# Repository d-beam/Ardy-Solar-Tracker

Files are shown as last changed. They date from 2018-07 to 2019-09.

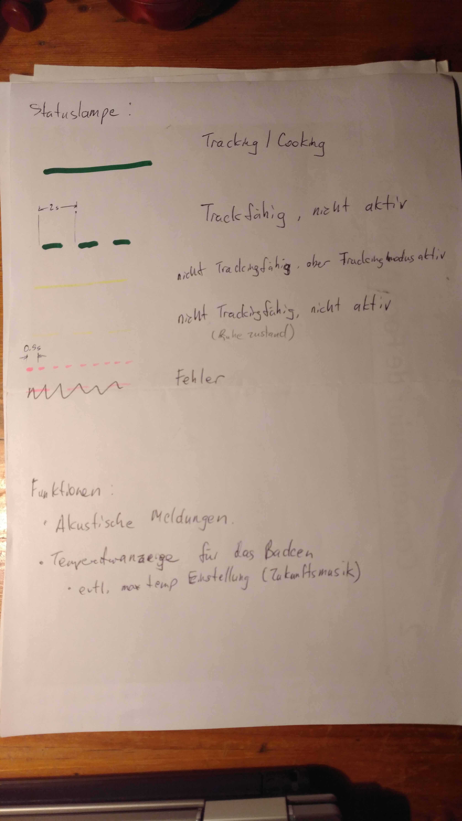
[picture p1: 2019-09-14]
docs/concepts/UI concept statusLED.jpg

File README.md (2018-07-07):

# Ardy-Solar-Tracker
2-axis Solar Tracker for concentrators and mirrors, supporting alt-az and Fixed Equatorial mechanisms, safe position

This project is started in June 2018 by the Technology Group at the Temera Healing Biotope in Colos, Portugal.  It is a Arduino based solar tracking controller with the following software features:

# Features
* support 2 axes, configurable also for use with only 1 (X) axis.
* support mechanisms working with Alt-Az or fixed equatorial coordinants and actuators
* support configuration of absolute positioning (open-loop), using only limit switches as positional feedback.
** Configuration of real time/date and installation orientation (home position) required.
* for each axis, read analog signals from 2 photodiodes and a signal representing the difference of the two diode signals for closed-loop control
* switch between open-loop and closed-loop control based on the reliability of the sensor signal
* Usage Modes: Idle, Tracking on, safe position
* automatically disable tracking below a certain elevation, or outside a defined range in hour-angle
* sensor polarity inversion, configurable
* travel limit switches, configurable as normally open or normally closed
* inversion of the orientation of each push button pair for each axis, configurable
* 2 speeds of motor control, with configurable dead bands
* push buttons for manual movements
* Modularity to allow changing motor controllers or RTC modules

It is written in Arduino code, but also with some C concepts such as pointers,
functions with pointer arguements, etc.

# Suggested Improvements:
* split up source code into multiple files for logical modularity
* improve very rough position estimator, which integrates the movement command over time for a positional change.
* add configurable offset for differential sensor signals

# Future directions:
* As solar cooking controller: setting of cooking time and maximum temperature
* logging of solar intensity

Contact Daniel Müller <dbmueller@gmx.net> for more information about the project, including the related electronics hardware.

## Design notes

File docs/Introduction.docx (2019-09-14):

# Open Source Solar Tracker

In the frame of a four-week technology seminar in Tamera Greg Fung, Christian Oekermann and Daniel Müller started the development of a microcontroller-based solar tracker.

The interest in that topic in Tamera mainly was raised from the Tamera-FixFocus project, where an analog sensor and electronics were used to control the two axis of the solar concentrator. This setup was limited in functionality and a digital modular solution based on the popular Arduino platform seem to be a good way to go forward.

Beside industrial applications the interest for solar tracking controllers also expands to other application fields, mainly towards solar cooking. Several tracked solar cookers are currently in use in Tamera and potentially could be controlled by the very same system to improve the usability greatly.

# General features

- 12-24 V input voltage
- Arduino based
- Modular system - Control board, motor drivers, real-time clock easily exchangeable
- Controles two axes (configurable for mounts based on Horizontal or equatorial coordinate systems)
- Homing with limit switches
- Support of different motor types (e.g. DC motors, stepper motors)
- Two stage tracking: Rough positioning by sun position algorithm when the sun doesn’t shine (open-loop control) and accurate tracking with photodiode sensor (closed-loop control) when the sun shines

# First application - Solar Tracker v0.1

The first implementation of the system is pretty much a copy of the analog tracking control system previously with the Tamera-FixFocus solar concentrator, but now comes with the capability of both closed-loop (sensor) tracking mode and open-loop tracking mode (using the sun position algorithm).

Download the files here

Discuss with the community here

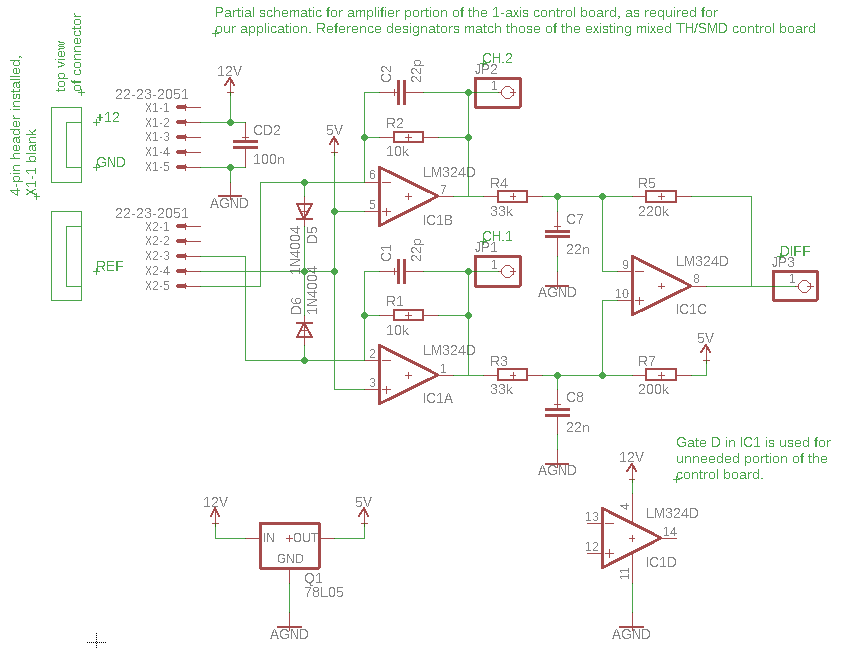
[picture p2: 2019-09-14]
docs/electronics/Sensor interface/sensor_interface_board_schematic.png

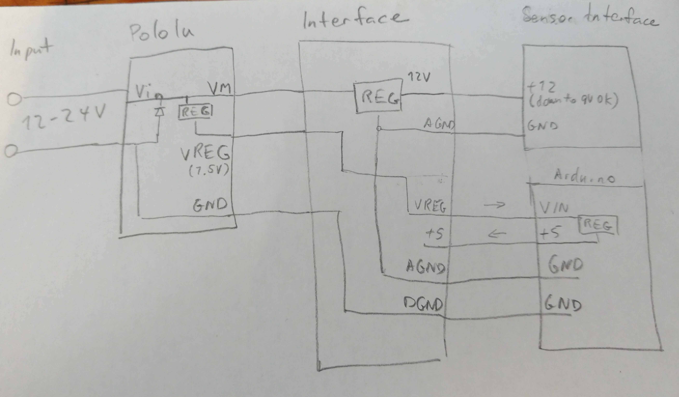
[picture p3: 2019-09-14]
docs/pictures/power concept.jpg

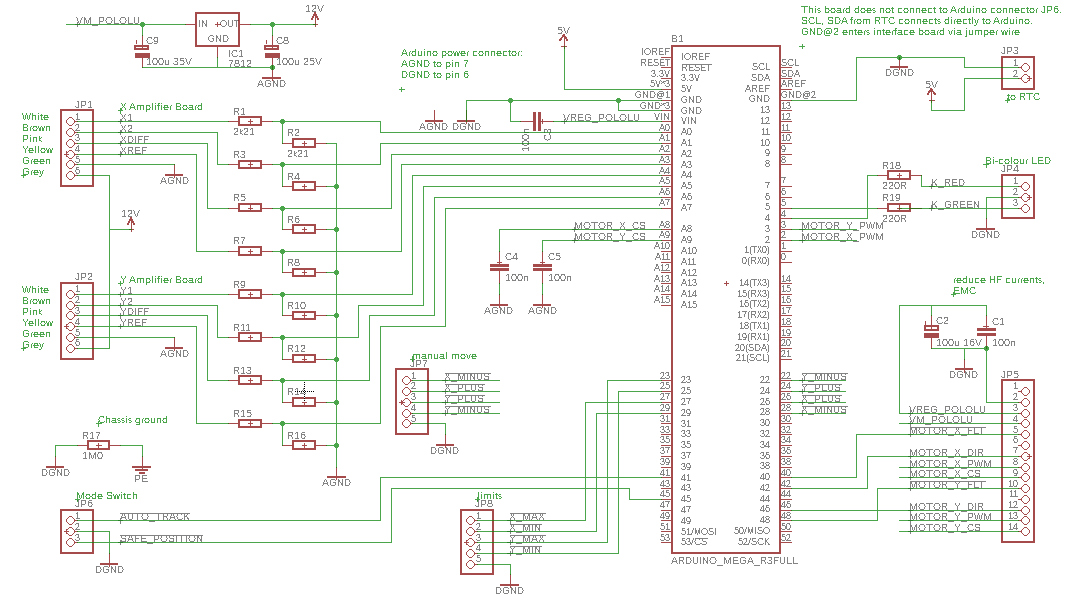
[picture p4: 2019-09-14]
docs/electronics/Interface shield/interface_board_schematic_v0_1.png

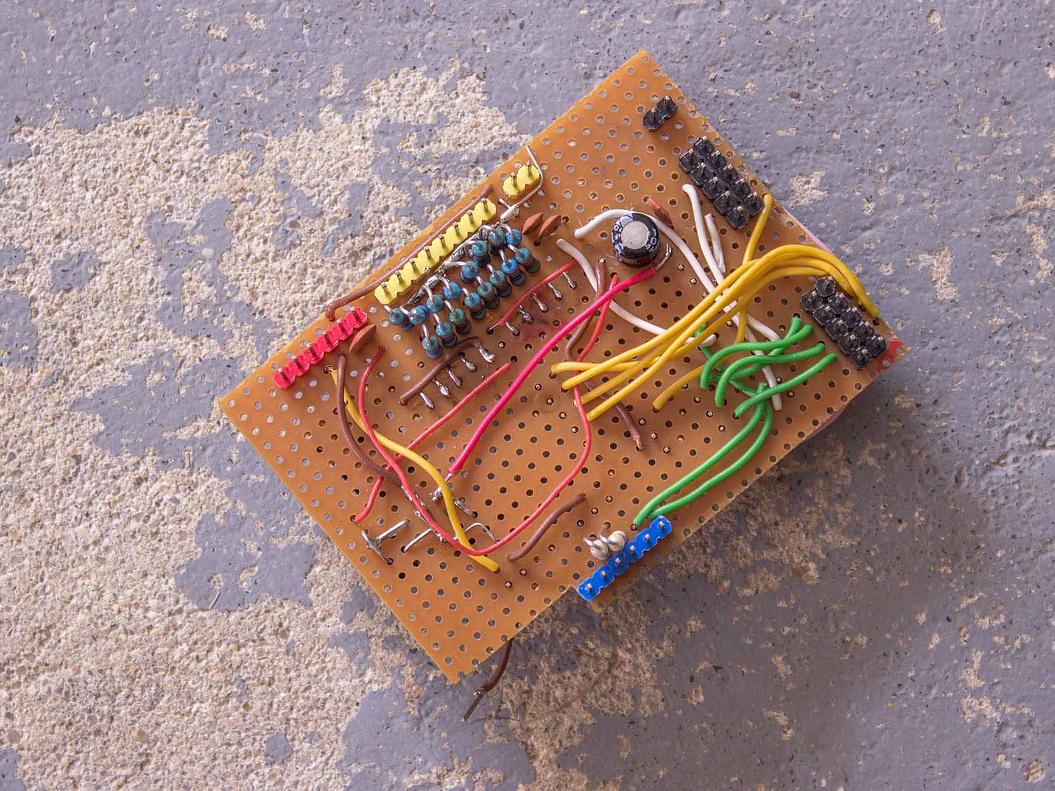
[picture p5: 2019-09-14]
docs/pictures/board_back.jpg

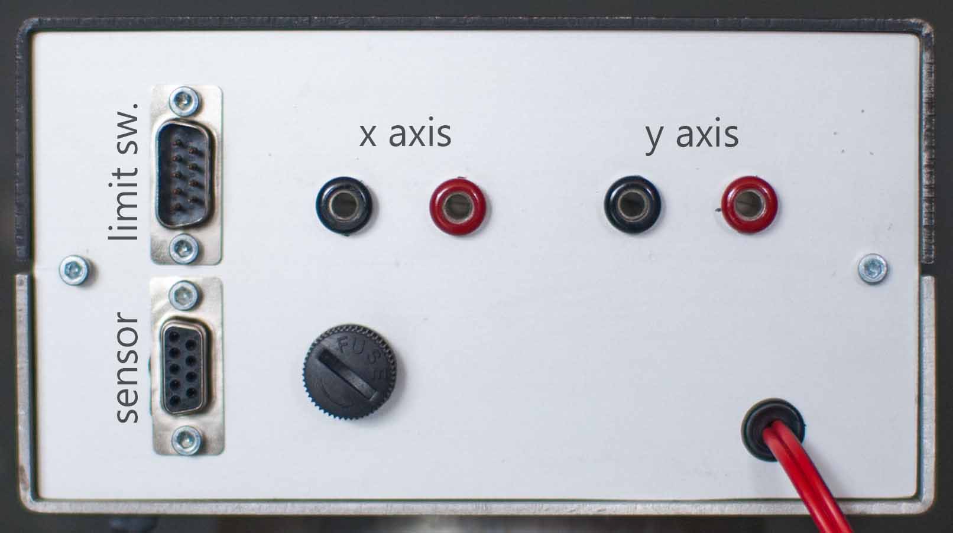
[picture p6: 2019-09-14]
docs/pictures/panel_front.jpg

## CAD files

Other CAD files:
docs/CAD models/Sensor.f3d

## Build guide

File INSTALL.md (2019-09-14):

Install/Build Instructions you will find in the docs folder

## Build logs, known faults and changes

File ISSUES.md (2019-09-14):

known issues 

21.03.2019
- When clouds come in, the mirror will move quite a bit, trying to “follow the sun”, before it switches to

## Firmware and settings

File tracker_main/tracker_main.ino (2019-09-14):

/******************************************************************************
    Solar Tracker: Application for Arduino
    settings for Tamera FixedFocus Mirror
    July 7, 2018 15:15 2018

    Update on 13.9.2019 
    - split into diffrent files 
     
    Gregory Fung <gwfung@gmail.com>
    Free for use under Creative Commons license CC BY:
   https://creativecommons.org/licenses/
 *****************************************************************************/
#include "DualG2HighPowerMotorShield.h"

#include <Wire.h>
#include <RTClib.h>
#include <math.h>
#include <Helios.h>   // Heliostat / Sun location library

// Local configuration
// Tamera: 37° 43' 7.2001'' N, 8° 31' 14.1924'' W
#define LATITUDE      37.7186667f     // [-90..90]
#define LONGITUDE     -8.520609f      // [-180..180)

// Application mode and settings --------------------
#define EQUATORIAL_AXES_MODE      true  // if false, output channels are Azimuth and elevation
// if false, output channels are X= tau hour angle and Y= delta declination
#define Y_AXIS_ACTIVE           true  // if false, all control functions except manual move is disabled for Y

#define OPEN_LOOP_POSITIONING_ENABLE  true  // if false, safe position and position initialization disabled.
// only tracking after rough manual alignment supported.

// Home position at min or max limit -----------
// true: homing at maximum position
// false: homing at mininum position
#define HOME_AT_MAX_X         false // morning, min tau position
#define HOME_AT_MAX_Y         true  // physically lowest position: summer, max delta

// Home position: --------------------
// The position of the system with minimum X and Y values, just before the limit switches are actuated.
// if EQUATORIAL_AXES_MODE, X is hour angle, Y is inclination
// if !EQUATORIAL_AXES_MODE, X is Azimuth, Y is elevation
#if EQUATORIAL_AXES_MODE
  #define HOME_POSITION_X           (-91.0) // °, morning position where low limit switches are located
  #define HOME_POSITION_Y           (23.5)  // ° where low limit switches are located
#else
  #define HOME_POSITION_X           (0.0)   // ° (north)
  #define HOME_POSITION_Y           (10.0)  // ° where low limit switches are located
#endif

// Safe position: --------------------
//Position for safe mode.  Must be within travel limits
#if EQUATORIAL_AXES_MODE
  #define SAFE_POSITION_X           (-90.0) // °
  #define SAFE_POSITION_Y           (23.0)  // °
#else
  #define SAFE_POSITION_X           (5.0)   // °
  #define SAFE_POSITION_Y           (11.0)  // °
#endif

// tracking active limitations: --------------------
// tracking will deactivate when the sun is calculated to be outside these ranges
#define SUN_ELEVATION_MIN_FOR_TRACKING      (10.0)  // °
#define SUN_HOUR_ANGLE_MIN_FOR_TRACKING     (-85.0) // °
#define SUN_HOUR_ANGLE_MAX_FOR_TRACKING     (85.0)  // °

// Manual move button polarity: --------------------
#define MANUAL_MOVE_POLARITY_FLIP_X       false   // true to invert control response, false otherwise
#define MANUAL_MOVE_POLARITY_FLIP_Y       true    // true to invert control response, false otherwise

// Limit switch action: --------------------
#define X_LIMIT_TRIP_SWITCH_N_O     true    // true: normally open switch, closes at limit
#define Y_LIMIT_TRIP_SWITCH_N_O     true    // true: normally open switch, closes at limit

// Sensor polarity: --------------------
#define SENSOR_POLARITY_FLIP_X      false   // true to invert control response, false otherwise
#define SENSOR_POLARITY_FLIP_Y      true    // true to invert control response, false otherwise

// Closed loop position sanity check: -------------------
#define CLOSED_LOOP_POSITIONING_SANITY_CHECK (false)      // true to enable comparison with calculated position

// Open loop position estimate: --------------------------
// Currently: Rectangular integration of motor movements commands
// set the steady-state movement speeds here, in °/s
#define MOTOR_SPEED_SLOW_PER_SEC_X      ((MOTOR_SPEED_FAST_PER_SEC_Y * POLOLU_SPEED_SLOW_Y) / POLOLU_SPEED_FAST_Y)    // speed ratiometric to Speed command?
#define MOTOR_SPEED_FAST_PER_SEC_X      0.54f   // °/s.  probably 10% accurate, needs further calibration
#define MOTOR_SPEED_SLOW_PER_SEC_Y      ((MOTOR_SPEED_FAST_PER_SEC_Y * POLOLU_SPEED_SLOW_Y) / POLOLU_SPEED_FAST_Y)    // °/s
#define MOTOR_SPEED_FAST_PER_SEC_Y      0.26f   // °/s.  probably 40% accurate, needs further calibration

// Control deadbands: --------------------------
// This reduces continual back and forth dithering due to slack in mechanical mechanism
//
// FAST_MOVE_DEADBAND: Within this much of the target location, stop using fast move speed
// CONTROL_DEADBAND: Within this much of the target location, stop moving
#define OPEN_LOOP_FAST_MOVE_DEADBAND_X    3   // °.
#define OPEN_LOOP_CONTROL_DEADBAND_X    0.3   // °
#define CLOSED_LOOP_FAST_MOVE_DEADBAND_X  500 // in raw diff ADC units (total range 2048, more than 1500 not recommended)
// Big setting to allow mechanism to decellerate and not overshoot
#define CLOSED_LOOP_CONTROL_DEADBAND_X    50    // in raw diff ADC units (total range 2048, more than 1500 not recommended)
#define CLOSED_LOOP_ABORT_LIMIT_X         25    // °, used for sanity check

#define OPEN_LOOP_FAST_MOVE_DEADBAND_Y    2   // °
#define OPEN_LOOP_CONTROL_DEADBAND_Y    0.3   // °
#define CLOSED_LOOP_FAST_MOVE_DEADBAND_Y  500 // in raw diff ADC units (total range 2048, more than 1500 not recommended)
#define CLOSED_LOOP_CONTROL_DEADBAND_Y    50  // in raw diff ADC units (total range 2048, more than 1500 not recommended)
#define CLOSED_LOOP_ABORT_LIMIT_Y         25  // °, used for sanity check


// movement delays: -------------------
// after stopping drive motors, how long to wait for mechanism to stop before proceeding
#define MOVE_STOP_FROM_FAST_DELAY (1000)    // ms
#define MOVE_STOP_FROM_SLOW_DELAY (1000)    // ms

// Closed loop tracking: -------------------
#define TRACKING_STABLE_COUNT       5       // count of loops before tracking stable is declared
                                            // used for position calibration

// Computation times: -------------------
// These constants may be used to integrate speed over time for position estimates
//
// Normal computation: happens every cycle of loop()
#define NORMAL_COMPUTATION_MS       (50)    // measured computational duration
// Extended computation: happens occassionally
#define EXTENDED_COMPUTATION_MS     (400)   // measured computational duration

// ******************************************************************************
// constants for internal operations, usually does not change between application
// ******************************************************************************

// Delay at the end of loop() before next cycle
#define UPDATE_DELAY_MS                 (250)
#define EXTENDED_COMPUTATION_COUNT      (60)

// Sensor limits, in raw 12-bit ADC units ------------
// ABS_MIN: below this level, sensor reading is not used.
//   lower to allow more tracking even if full cloudy,
//   may cause problems with background light when pointed away from sun
//   raise to use open loop calculated more often when cloudy
#define SENSOR_ABS_MIN      300       // 250 accepts signal levels when cloudy
                                      //~900 have been seen in full sun
// ABS_MAX: unrealistically strong sensor level
#define SENSOR_ABS_MAX      1800      // set >4096 to effectively disable checking
// REF: reference level of analog circuitry, which is also read by an ADC channel
#define SENSOR_REF_DEFAULT  2048      // half of full scale
#define SENSOR_REF_MAX      2248      // min resaonable ref value
#define SENSOR_REF_MIN      1848      //

// Initialization ------------
// This many loops are ran before tracking will begin, to allow analog inputs to settle.
#define SENSOR_INIT_LOOP_COUNT    (16)

// Arduino GPIO numbers: analog inputs ----------------
#define AI_X1ABS            0
#define AI_X2ABS            1
#define AI_XDIFF            2
#define AI_XREF             3
#define AI_Y1ABS            4
#define AI_Y2ABS            5
#define AI_YDIFF            6
#define AI_YREF             7
#define AI_MOTOR_CURRENT_X  8
#define AI_MOTOR_CURRENT_Y  9

// Arduino GPIO numbers: digital ---------------
// 0, 1 used for serial comms
#define DO_MOTOR_PWM_X      2
#define DO_MOTOR_PWM_Y      3
#define DO_STATUS_LED_RED   4
#define DO_STATUS_LED_GREEN 5

#define DI_MODE_SAFE          43
#define DI_MODE_TRACK         41
#define DI_LIMIT_SWITCH_X_MAX 27
#define DI_LIMIT_SWITCH_X_MIN 29

//normal configration:
//#define DI_LIMIT_SWITCH_Y_MAX   23
//#define DI_LIMIT_SWITCH_Y_MIN   25
//compensating for wiring error on Tamera fixed-focus
#define DI_LIMIT_SWITCH_Y_MAX   25
#define DI_LIMIT_SWITCH_Y_MIN   23

#define DI_MANUAL_MOVE_X_PLUS   26
#define DI_MANUAL_MOVE_X_MINUS  28
#define DI_MANUAL_MOVE_Y_PLUS   24
#define DI_MANUAL_MOVE_Y_MINUS  22

// If motor PWM assignments match default config from
// pololu shield, timer1 can be used for PWM:  M1 9, M2 10
#define DO_MOTOR_DIR_X    42
#define DI_MOTOR_FAULT_X  40
#define DO_MOTOR_DIR_Y    46
#define DI_MOTOR_FAULT_Y  48

// unused, but referenced by motor driver
#define DO_MOTOR_SLEEP_X  47
#define DO_MOTOR_SLEEP_Y  45


// Serial Monitor debug output selection
// #define SERIAL_PLOTTER_FORMAT  // define for serial plotting csv format, disables labels
// #define SERIAL_DEBUG_RAW_SENSOR  // define to print raw sensor values
#define SERIAL_DEBUG_SUN_CALC   // define to enable

/******************************************************************************
   Global Variables
******************************************************************************/

// Using custom constructor here to specify non-default pin assignment
// Note the exact model of the sheild is in the type name and may need adjustment
// see https://github.com/pololu/dual-g2-high-power-motor-shield/
// TODO generic version DualG2HighPowerMotorShield?  current sensing gain info would not be encapsulated.
DualG2HighPowerMotorShield18v18 md(
  DO_MOTOR_SLEEP_X, DO_MOTOR_DIR_X,
  DO_MOTOR_PWM_X, DI_MOTOR_FAULT_X, AI_MOTOR_CURRENT_X,
  DO_MOTOR_SLEEP_Y, DO_MOTOR_DIR_Y,
  DO_MOTOR_PWM_Y, DI_MOTOR_FAULT_Y, AI_MOTOR_CURRENT_Y);
RTC_DS1307 rtc;
Helios sunPosition;

// actual date/time in UTC
DateTime actualTime;

// X axis---------------
int sensorX1RawAbs;
int sensorX2RawAbs;
int sensorXRawDiff;
int sensorXRawRef = SENSOR_REF_DEFAULT;
int sensorX1Level;
int sensorX2Level;
int sensorXDiff;
bool sensorLevelsOkX = false;
int motorSettingX = 0;
int motorCurrentX = 0;
bool atLimitXMax;
bool atLimitXMin;

bool closedLoopActiveX = false;
bool closedLoopFaultX = false;
bool trackingLockedX = false;
int trackingStableCounterX = 0;

double targetAzimuth;
float errorPositionX;     // position error for X in open loop mode
float actualPositionX;
double targetPositionX;
int errorClosedLoopX;     // control error for X, int because using raw ADC units


// Y axis--------------------
int sensorY1RawAbs;
int sensorY2RawAbs;
int sensorYRawDiff;
int sensorYRawRef = SENSOR_REF_DEFAULT;
int sensorY1Level;
int sensorY2Level;
int sensorYDiff;
bool sensorLevelsOkY = false;
int motorSettingY = 0;
int motorCurrentY = 0;
bool atLimitYMax;
bool atLimitYMin;

bool closedLoopActiveY = false;
bool closedLoopFaultY = false;
bool trackingLockedY = false;
int trackingStableCounterY = 0;

double targetElevation;
float errorPositionY;     // position error for Y in open loop mode
float actualPositionY;
double targetPositionY;
int errorClosedLoopY;     // control error for Y, int because using raw ADC units


// both axis--------------------
bool sensorInitDone = false;
bool generalFault = false;
bool userInputFault = false;
bool trackingRequested = false;   // user input
bool trackingActive = false;    // possible and active
bool safePositionCmd = false;
bool positionInitialized = false;
bool manualMoveXPlus = false;
bool manualMoveXMinus = false;
bool manualMoveYPlus = false;
bool manualMoveYMinus = false;
int slowUpdateCountdown = 0;

// LED
#define LED_COLOUR_OFF    0
#define LED_COLOUR_RED    1
#define LED_COLOUR_GREEN  2
#define LED_COLOUR_YELLOW 3

#define LED_BLINK_STEADY  0
#define LED_BLINK_SLOW    1
#define LED_BLINK_FAST    2

int ledColour = 0;
int ledBlink = 0;
bool ledActualState = false;
int ledActualColour = 0;
bool rtcOK = false;

const int ledBlinkInterval = 1000;      // ms, half of cycle
unsigned long previousLedMillis = 0;        // will store last time LED was updated

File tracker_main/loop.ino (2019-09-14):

/******************************************************************************
   Main scan loop for Solar Tracker
   by:      Gregory Fung <gwfung@gmail.com>
*/

void loop() {
  int testCount = 0;
  static bool lastSafePositionCmd = false;

  lastSafePositionCmd = safePositionCmd;
  readUserInputs();

  // calculations that are only needed infrequently
  if (--slowUpdateCountdown <= 0 || (lastSafePositionCmd != safePositionCmd)) {
    slowUpdateCountdown = EXTENDED_COMPUTATION_COUNT;
    actualTime = timeNow();
    if (safePositionCmd) {
      // TODO time dependent safe position?
      targetPositionX = SAFE_POSITION_X;
      targetPositionY = SAFE_POSITION_Y;
    } else {
      calculateSunLocation(actualTime, sunPosition, LONGITUDE, LATITUDE,
                           &targetPositionX, &targetPositionY);

      // save possibly intermediate results
      targetAzimuth = targetPositionX;
      targetElevation = targetPositionY;

      /* RTC */
      writeDebugOutputTime(actualTime);

      /* Sun Position */
#ifdef SERIAL_DEBUG_SUN_CALC
      Serial.print(", Sun at Azi ");
      Serial.print(targetAzimuth);
      Serial.print(", Elev ");
      Serial.print(targetElevation);
#endif
      if (EQUATORIAL_AXES_MODE) {
        convertToStableEquatorialAxes(LATITUDE, targetAzimuth, targetElevation, &targetPositionX, &targetPositionY);
      }
#ifdef SERIAL_DEBUG_SUN_CALC
      Serial.println("");
#endif
    }
    updatePosition(EXTENDED_COMPUTATION_MS);
  }
  errorPositionX = actualPositionX - targetPositionX;
  errorPositionY = actualPositionY - targetPositionY;

  // Can we track right now?
  trackingActive  = trackingRequested;
  if (targetElevation < SUN_ELEVATION_MIN_FOR_TRACKING) {
    trackingActive = false;
  }
  if (EQUATORIAL_AXES_MODE) {
    if ((targetPositionY < SUN_HOUR_ANGLE_MIN_FOR_TRACKING) ||
        (targetPositionY > SUN_HOUR_ANGLE_MAX_FOR_TRACKING)) {
      trackingActive = false;
    }
  }

  // TODO: maximum temperature control: if at limit, aim for non-optimal position by
  // adding offset to targetPositionX?

  // reading Sensors -------------------------------------------------------
  readTrackingSensorsX();
  sensorLevelsOkX = CheckSensorLevels(&sensorXRawRef, SENSOR_REF_DEFAULT,
                                      &sensorX1RawAbs, &sensorX2RawAbs, &sensorXRawDiff,
                                      &sensorX1Level, &sensorX2Level, &sensorXDiff,
                                      SENSOR_ABS_MIN, SENSOR_ABS_MAX);
  readTrackingSensorsY();
  sensorLevelsOkY = CheckSensorLevels(&sensorYRawRef, SENSOR_REF_DEFAULT,
                                      &sensorY1RawAbs, &sensorY2RawAbs, &sensorYRawDiff,
                                      &sensorY1Level, &sensorY2Level, &sensorYDiff,
                                      SENSOR_ABS_MIN, SENSOR_ABS_MAX);

  // Closed loop and manual control-------------------------------------------------------
  readTravelLimits();
  if (!trackingRequested && !safePositionCmd) {
    manualMotorControl();
  } else {
    closedLoopMotorControl();
  } //endif manual or closed loop automatic

  // open loop position estimate calibration:
  // if trackingLocked, we could update our position estimate to the actual expected position of the sun?
  // this is OK, possibly except:
  // 1. where there is a fault of a "false sun" that we have tracked (ie reflection?)
  if (trackingLockedX && (trackingLockedY || !Y_AXIS_ACTIVE)) {
    // update estimated actual position with expected position
    actualPositionX = targetPositionX;
    actualPositionY = targetPositionY;
    positionInitialized = true;
    //Serial.println("position initialized using tracking lock and expected sun position");
  }

  //Open loop positioning ---------------------------------------------------
  readTravelLimits();
  if (generalFault) {
    // unexpected?  TODO improve handling
    driveX(MOTOR_DIR_MINUS, MOTOR_SPEED_OFF);
  } else {
    openLoopMotorControl();
  }   //endif generalFault

  // Fault handling ---------------------------------------------------
  if (!areMotorsOK()) {
    // TODO better handling
    generalFault = true;
  }

  if (closedLoopFaultX) {
    //Reinitialize? up to 3 times?
  }
  if (closedLoopFaultY) {
    //Reinitialize? up to 3 times?
  }

  // System maintanence ---------------------------------------------------
  setStatusLed();
  ledStateUpdate();
  updatePosition(UPDATE_DELAY_MS + NORMAL_COMPUTATION_MS);
  writeDebugOutput();
  delay(UPDATE_DELAY_MS);
}

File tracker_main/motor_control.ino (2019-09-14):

/******************************************************************************
   Motor Control
******************************************************************************/

#define MOTOR_DIR_PLUS      (true)
#define MOTOR_DIR_MINUS     (false)
#define MOTOR_SPEED_FAST    (2)
#define MOTOR_SPEED_SLOW    (1)
#define MOTOR_SPEED_OFF     (0)

#define MOTOR_CURRENT_LIMIT_X   (8000)    // mA
#define MOTOR_CURRENT_LIMIT_Y   (18000)   // mA

/* development model
  #define POLOLU_SPEED_FAST_X   (400) // pololu max 400
  #define POLOLU_SPEED_SLOW_X   (25)  // pololu max 400
  #define POLOLU_SPEED_FAST_Y   (400) // pololu max 400
  #define POLOLU_SPEED_SLOW_Y   (25)  // pololu max 400
*/
/* Tamera FixFocus */
// pololu maxinum 400
#define POLOLU_SPEED_FAST_X   (400) //
#define POLOLU_SPEED_SLOW_X   (100) // 
#define POLOLU_SPEED_FAST_Y   (300) // fast enough and reduces current spikes
#define POLOLU_SPEED_SLOW_Y   (250) //

/******************************************************************************
    Checks for motor faults and handles as required.  Based on demo from pololu.
    by:     Gregory Fung <gwfung@gmail.com>

    Returns:    false on motor fault input or overcurrent, true otherwise.
    Postcondition:
      Motor drivers disabled
*/
bool areMotorsOK() {
  bool ok = true;
  motorCurrentX = md.getM1CurrentMilliamps();
  //motorCurrentX = 0;
  if (motorCurrentX > MOTOR_CURRENT_LIMIT_X || md.getM1Fault()) {
    md.disableM1Driver();
    delay(1);
    ok = false;
    if (md.getM1Fault()) {
      Serial.println("Motor X (M1) fault");
    } else {
      Serial.println("Motor X (M1) overcurrent");
    }
  }
  motorCurrentY = md.getM2CurrentMilliamps();
  //motorCurrentY = 0;
  if (motorCurrentY > MOTOR_CURRENT_LIMIT_Y || md.getM2Fault()) {
    md.disableM2Driver();
    delay(1);
    ok = false;
    if (md.getM1Fault()) {
      Serial.println("Motor Y (M2) fault");
    } else {
      Serial.println("Motor Y (M2) overcurrent");
    }
  }
  return ok;
}

/******************************************************************************
    Starts movement of the tracker in the X axis, in the given direction at the given speed.
    if movement was already active in the opposite direction, movement shall be stopped.
    by:     Gregory Fung <gwfung@gmail.com>

    Parameters:
      direction: true in positive direction, false in negative direction
      speed: 0: stop, 1 slow, 2 fast
    Precondition:
    Postcondition:
      targetPositionX: azimuth in degrees [0..360)
      targetPositionY: elevation in degrees [-90..90)
*/
void driveX(bool direction, int speed) {
  int pololuSpeed = 0;
  static bool lastDirection = false;

  // if driver was off before
  if ((speed > 0) && (motorSettingX == 0)) {
    md.enableM1Driver();
    delay(1);  // The drivers require a maximum of 1ms to elapse when brought out of sleep mode.
  }

  // stop first if changing directions
  if ((speed > 0) && (direction != lastDirection)) {
    speed = 0;
  }

  // TODO consider speed ramp up and ramp down?
  if (speed >= 2) {
    pololuSpeed = POLOLU_SPEED_FAST_X;
  } else if (speed == 1) {
    pololuSpeed = POLOLU_SPEED_SLOW_X;
  } else {
    pololuSpeed = 0;
  }

  lastDirection = direction;  //update last motor setting memory
  motorSettingX = speed;
  if (!direction) {
    pololuSpeed = -1 * pololuSpeed;
    motorSettingX = -1 * speed;
  }

  // drive motor
  md.setM1Speed(pololuSpeed);

  if (speed == 0) {
    md.disableM1Driver();
  }
}

/******************************************************************************
    Starts movement of the tracker in the Y axis, in the given direction at the given speed.
    if movement was already active in the opposite direction, movement shall be stopped.
    by:     ?

    Parameters:
      direction: true in positive direction, false in negative direction
      speed: 0: stop, 1 slow, 2 fast
    Precondition:
    Postcondition:
*/
void driveY(bool direction, int speed) {
  int pololuSpeed = 0;
  static bool lastDirection = false;

  // if driver was off before
  if ((speed > 0) && (motorSettingY == 0)) {
    md.enableM2Driver();
    delay(1);  // The drivers require a maximum of 1ms to elapse when brought out of sleep mode.
  }

  // stop first if changing directions
  if ((speed > 0) && (direction != lastDirection)) {
    speed = 0;
  }

  // TODO consider speed ramp up and ramp down?
  if (speed >= 2) {
    pololuSpeed = POLOLU_SPEED_FAST_Y;
  } else if (speed == 1) {
    pololuSpeed = POLOLU_SPEED_SLOW_Y;
  } else {
    pololuSpeed = 0;
  }

  lastDirection = direction;  //update last motor setting memory
  motorSettingY = speed;
  if (!direction) {
    pololuSpeed = -1 * pololuSpeed;
    motorSettingY = -1 * speed;
  }
  // drive motor
  md.setM2Speed(pololuSpeed);
  if (speed == 0) {
    md.disableM2Driver();
  }
}

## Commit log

2018-07-07 correct limit switch GPIO, improve comments based on review
2019-09-13 adding documentation from v0.1 includes pic and docs
    [Mega_interface.sch, Sensor.f3d, sensor_interface.sch]
